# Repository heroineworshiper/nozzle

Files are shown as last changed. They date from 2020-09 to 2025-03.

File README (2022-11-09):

F-35 NOZZLE
Copyright (C) 2020-2022 Adam Williams <broadcast at earthling dot net>

This program is free software; you can redistribute it and/or modify
it under the terms of the GNU General Public License as published by
the Free Software Foundation; either version 2 of the License, or
(at your option) any later version.

This program is distributed in the hope that it will be useful,
but WITHOUT ANY WARRANTY; without even the implied warranty of
MERCHANTABILITY or FITNESS FOR A PARTICULAR PURPOSE.  See the
GNU General Public License for more details.

You should have received a copy of the GNU General Public License
along with this program; if not, write to the Free Software
Foundation, Inc., 59 Temple Place, Suite 330, Boston, MA  02111-1307  USA

What you'll find here:

nozzle.pcb - obsolete layout of the electronicals
nozzle.X - obsolete firmware for the electronicals

nozzle.c - atmega328 firmware for common motor controller
nozzle5.pcb - layout of common motor controller

export*.FCMacro: obsolete scripts

final.FCStd - print tube segments with motor attachments

monitor.c - dump debugging statements from serial port without motor polling commands

motor2.FCStd - latest motor assembly

base.FCStd - base + electronical platform

bearing2.FCStd - latest bearing parts.  
    Mane gear must be 2 parts to be installed.
    Print mane gear ORed with print mask.  Print mask must be rotated 180 deg 
    not cut in order to get the horizontal expansion gap.
    Print bearing inner, bearing outer

tube.c - generate isogrid tubes

elbow1.FCStd: model for elbow1 & elbow3 segments
 - the 2 elbow segments with motors use identical tube sections
 - must transfer to final.FCStd & print with motor mounts
 - subtract inside from motor mount but don't print it
 - remove support after printing

elbow2.FCStd: print to get elbow2
    - support is on opposite side as elbow1
    - remove support after printing
    - must glue elbow2 & elbow3 so the short & long sides line up

exit.c - generate the exit nozzle to be combined with exit.FCStd
    Run exit to generate exit.stl

exit.FCSTd:
    - print tube & exit separately from here
    - remove support after printing
    - clip off chevron support

final.FCStd: print segments with motors from here
    - inlet + inlet motor mount
    - elbow1 + elbow1 motor mount
    - elbow3 + elbow3 motor mount
    - other segments are only shown to aid alignment
    - must glue elbow2 & elbow3 so the short & long sides line up

inlet.FCStd: model for inlet segment
    - must transfer to final.FCStd & print with motor mount

3dstuff.h - common 3D functions

--------------------------------------------------------------------------------
Programming the common motor controller:

Set the board number in nozzle.h
make clean

Program the bootloader
make nozzle_fuse
make bootloader_isp

--------------------------------------------------------------------------------
Previous notes:

This design used leftover motors without encoders from polulu.  An
easier design would use gearmotors with built in encoders from
adafruit.com.  Lighter motors are better.  100:1 or more is better.

The latest versions of each part are listed here.
25% infill

standalone motor parts:
     - print with no raft
     - 50% infill
     - Support must be everywhere instead of just touching base
    motor2.FCStd
        pinion
        top platform
        strap
         - Print the laminations perpendicular to the motor axis

tubes with motor parts:
    final.FCStd
        inlet
        elbows
        oblique or straight bottom base depending on the tube section
        tube section
         - Tubes must be printed with the tapered overhang on top.
         - Print with a brim & support to aid the 1mm alignment rings
        cable guards
         - Only needed for 2 motors.
         - hot glued on
         - Print the laminations perpendicular to the motor axis
         - use a brim to aid separating the support

bearing parts:
     - print with no raft or support to get flat sides
    bearing.FCStd
        split mane gear with 2 different gear splitters to get 2 halves
        bearing inner
        bearing outer

base:
    no support
    skirt adhesion
    base.FCStd
        base
        electronicals + screw holes

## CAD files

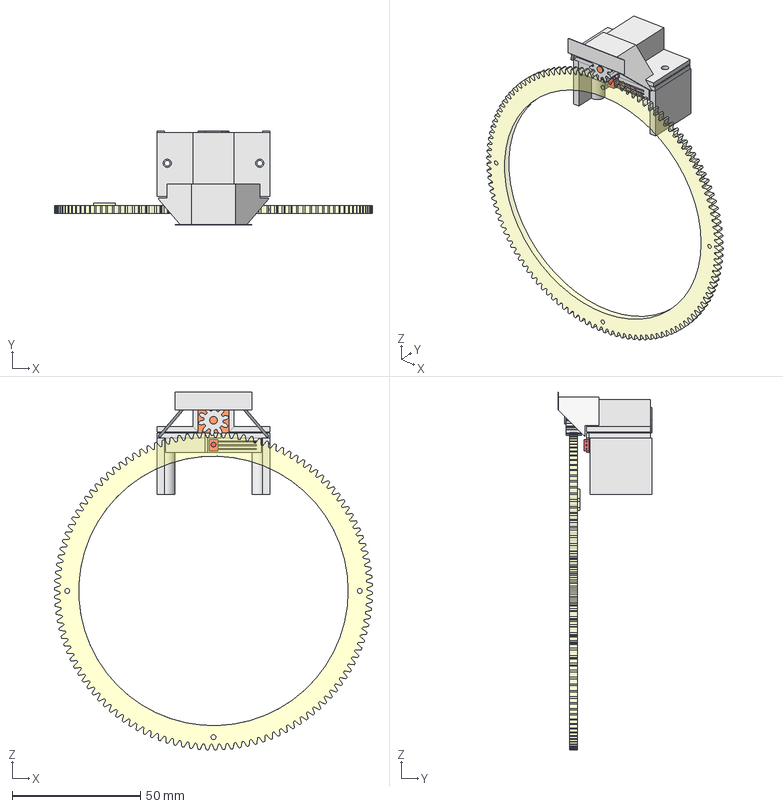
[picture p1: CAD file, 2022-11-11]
motor2.FCStd
124.0 x 36.5 x 139.5 mm
motor001
pinion gear
hall006
mane gear
cable shroud
motor strap
motor stand
motor base

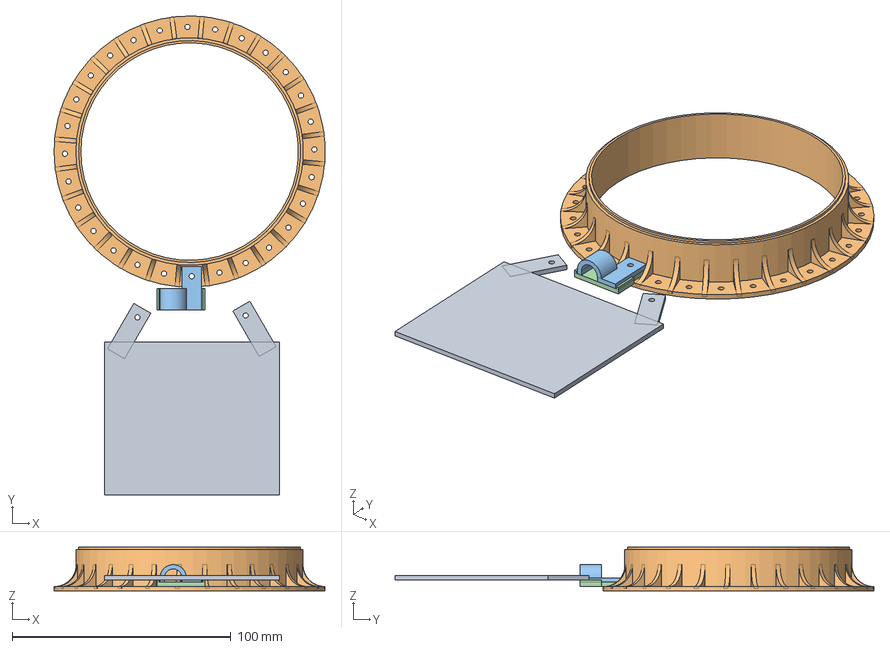
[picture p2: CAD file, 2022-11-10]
base.FCStd
123.9 x 219.0 x 20.0 mm
electronicals + screw holes
base
cable1
cable2

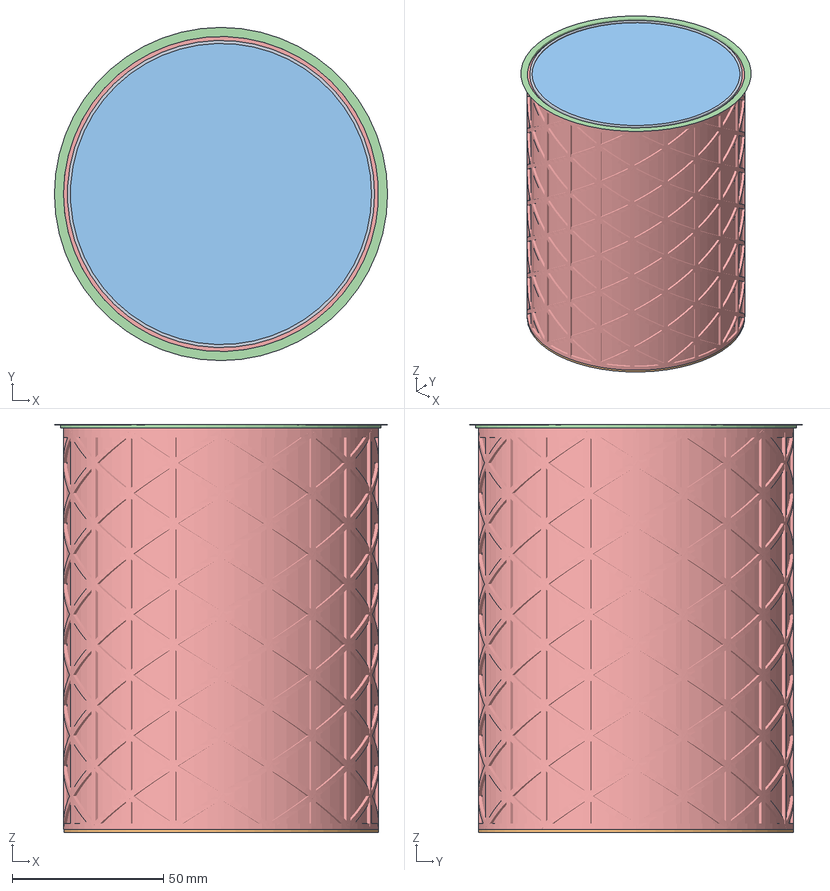
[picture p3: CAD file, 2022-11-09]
inlet.FCStd
110.0 x 110.0 x 134.7 mm
Thickness
overlap015
inside
support
inlet

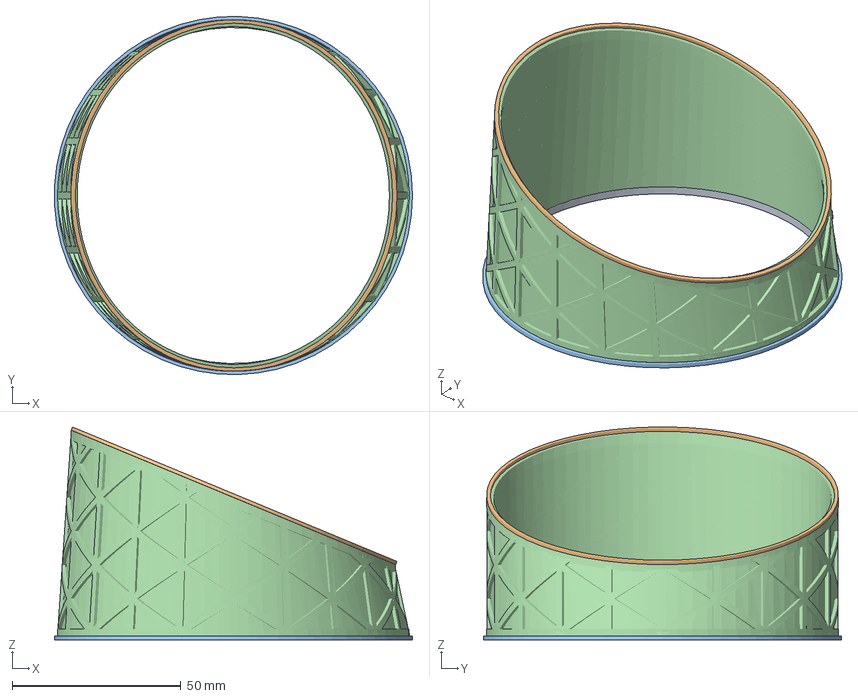
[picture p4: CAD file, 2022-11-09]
elbow2.FCStd
105.9 x 106.0 x 63.0 mm
overlap002
overlap001
support001
elbow

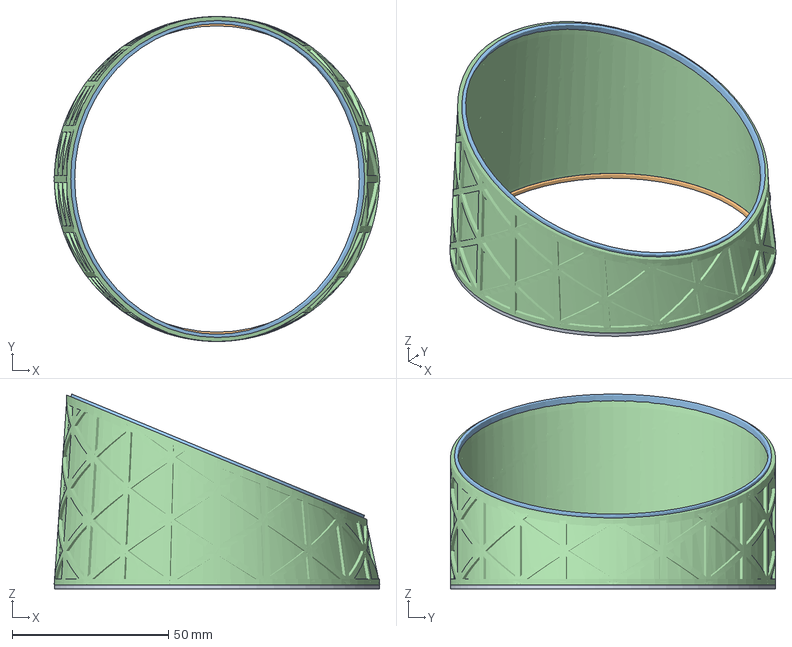
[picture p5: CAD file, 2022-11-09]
elbow1.FCStd
104.2 x 104.0 x 62.4 mm
overlap001
support
elbow

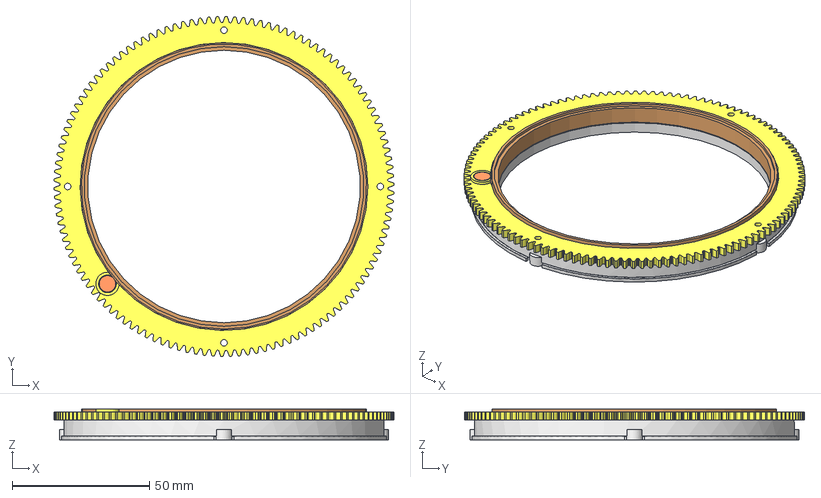
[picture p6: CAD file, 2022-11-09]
bearing2.FCStd
124.0 x 124.0 x 11.2 mm
mane gear
magnet002
bearing inner001
bearing outer003

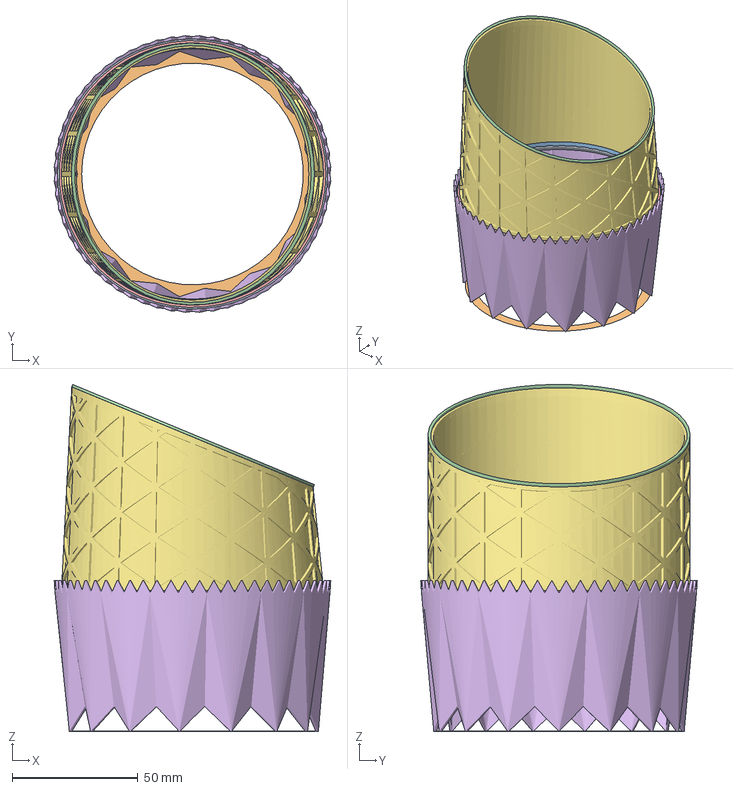
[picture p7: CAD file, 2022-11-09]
exit.FCStd
109.8 x 109.8 x 137.8 mm
support001
overlap009
overlap008
exit003
outlet

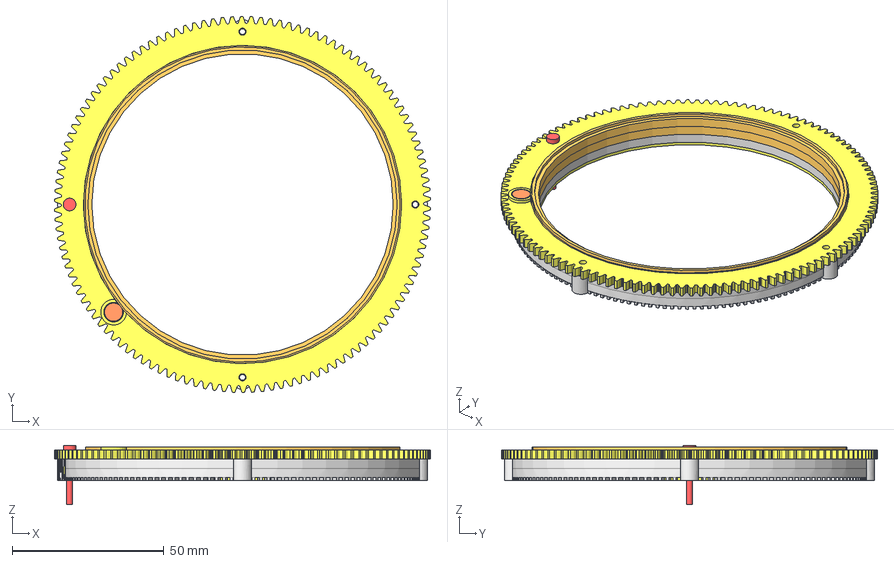
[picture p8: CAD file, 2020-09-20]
bearing.FCStd
124.0 x 124.0 x 19.6 mm
screw001
mane gear
magnet002
bottom thickness
top thickness
top overlap
bottom overlap
strut
bearing outer + screw holes

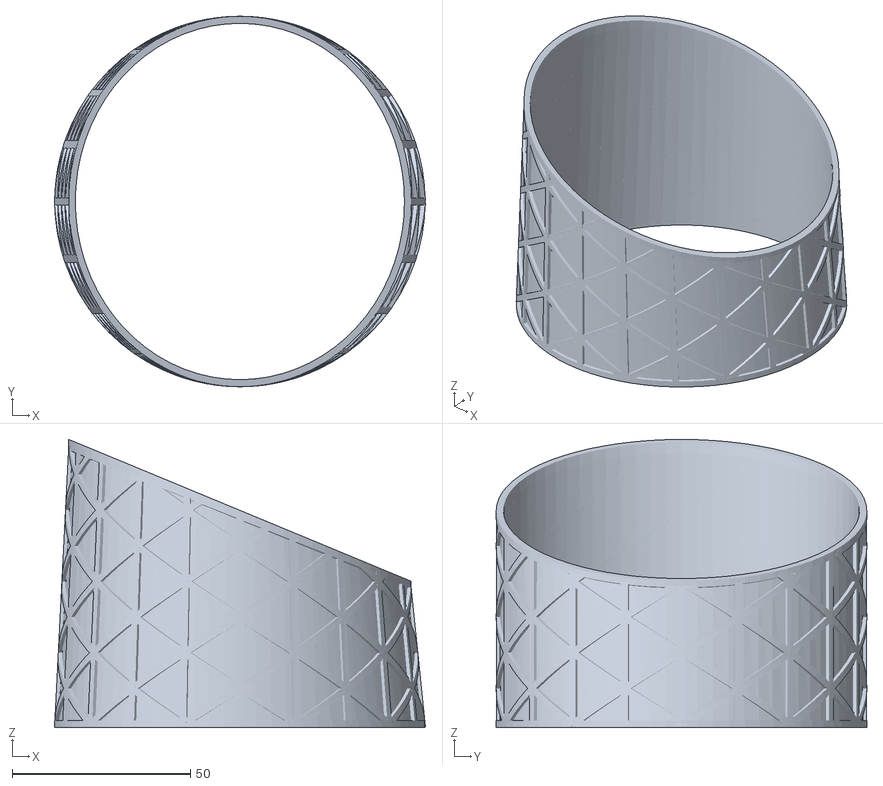
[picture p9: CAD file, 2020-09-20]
outlet.stl
104.1 x 104.0 x 80.9

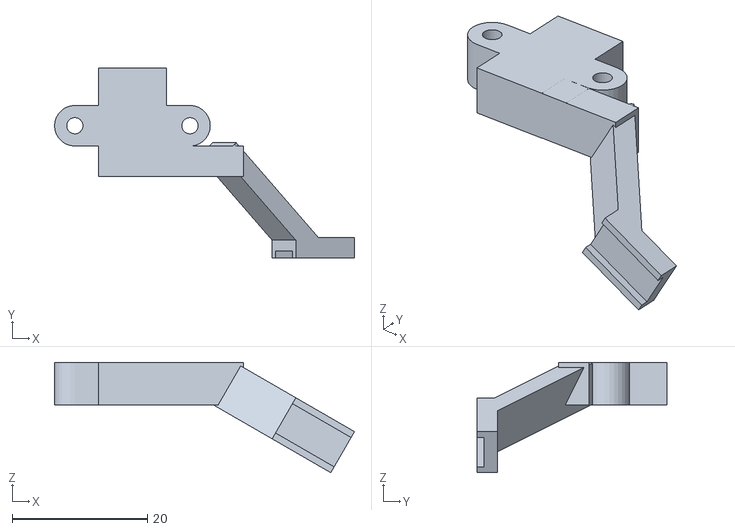
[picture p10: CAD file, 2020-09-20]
top_base.stl
44.3 x 28.0 x 16.3

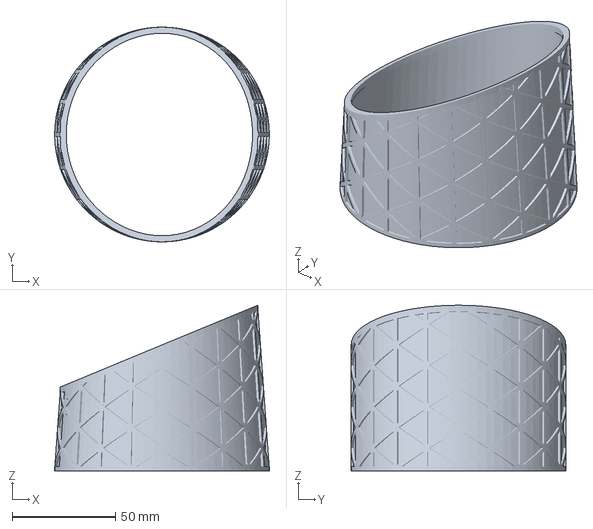
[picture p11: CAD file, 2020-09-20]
elbow4.3mf
104.1 x 104.0 x 80.2 mm

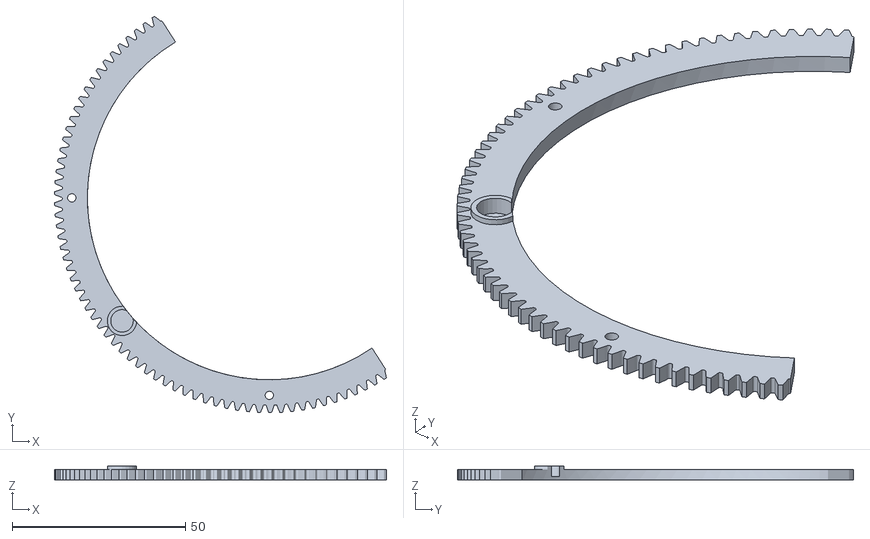
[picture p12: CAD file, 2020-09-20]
mane_gear1.stl
95.8 x 114.4 x 4.00

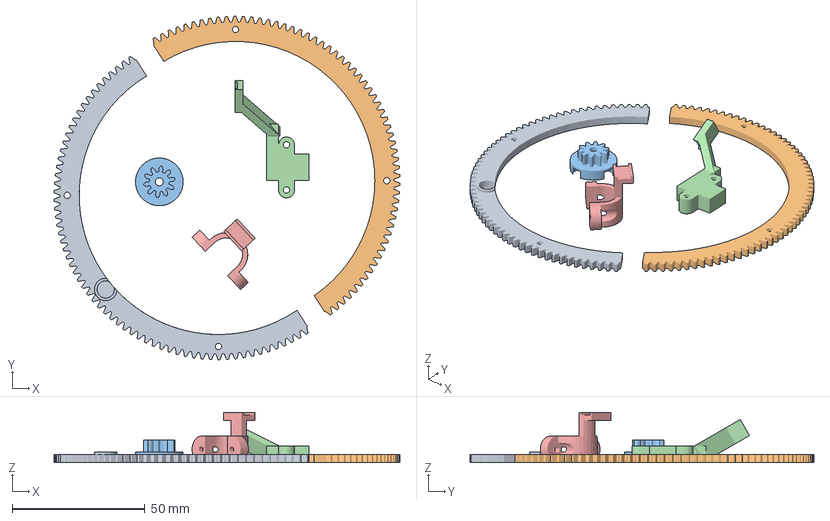
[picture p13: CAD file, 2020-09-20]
mane_gear.3mf
130.5 x 129.5 x 19.0 mm
mane_gear1.stl
mane_gear2.stl
pinion.stl
top_platform.stl
strap.stl

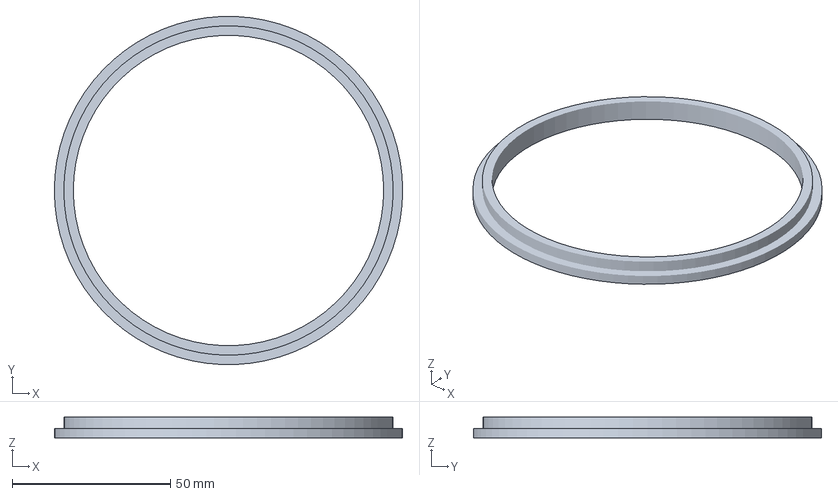
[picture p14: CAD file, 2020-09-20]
bearinginner.3mf
110.0 x 109.9 x 6.50 mm

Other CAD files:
top_platform.stl
bearingouter.stl
cableguard.stl
electronicals.stl
base.stl
bearinginner.stl
bodge.stl
bottom_base.stl
elbow.FCStd
elbow.stl
elbow1.3mf
elbow1.stl
elbow2.3mf
elbow2.stl
elbow3.3mf
elbow3.stl
elbow4.stl
exit.3mf
exit.stl
exit_elbow.stl
hall.FCStd
inlet.3mf
inlet.stl
mane_gear.stl
mane_gear2.stl
motor.FCStd
strap.stl
test.stl
tube.stl
tube2.stl

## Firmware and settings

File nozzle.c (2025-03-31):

/*
 * F-35 COMMON NOZZLE BOARD
 * Copyright (C) 2020-2025 Adam Williams <broadcast at earthling dot net>
 * 
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
 */

// this runs on each control board
// make board0.hex
// make board1.hex
// make board2.hex
// make nozzle_fuse
// make board0_isp
// make board1_isp
// make board2_isp

// disable this to try to reduce encoder drift
//#define ENABLE_DEBUG
// disable this to actually see the debugging output
#define ENABLE_POLLING


#include "uart.h"
#include "nozzle.h"
#include "table.h"

#include <inttypes.h>
#include <avr/io.h>
#include <avr/pgmspace.h>
#include <avr/interrupt.h>
#include <avr/wdt.h>
#include <util/delay.h>

#define TOGGLE_LED PORTB ^= (1 << DDB5);
#define LED_DELAY (HZ / 2)
#define LED_DELAY2 (HZ / 4)

// boundary sensor
#define HALL_THRESHOLD 16
#define HALL_CENTER 127

// ticks to wait for a motor to stop
#define MOTOR_DELAY (HZ / 2)

#if BOARD == 0
// IR code follows.  Improved version of heroineclock 2
typedef struct
{
    const uint8_t *data;
    const uint8_t value;
} ir_code_t;

// remote control codes.  Discard 1st & last symbol received since we
// only capture the rising edge.
const uint8_t up_data[] = 
{ 4,4,1,4,1,1,1,1,4,1,4,1,4,4,4,4,1,4,4,4,1,1,4,1,4,1,1,1,4,4,1,4,1 };
const uint8_t down_data[] = 
{ 4,4,1,4,1,1,1,1,4,1,4,1,4,4,4,4,1,1,4,4,1,1,4,1,4,4,1,1,4,4,1,4,1 };
const uint8_t left_data[] = 
{ 4,4,1,4,1,1,1,1,4,1,4,1,4,4,4,4,1,1,1,4,4,1,4,1,4,4,4,1,1,4,1,4,1 };
const uint8_t right_data[] = 
{ 4,4,1,4,1,1,1,1,4,1,4,1,4,4,4,4,1,4,1,4,4,1,4,1,4,1,4,1,1,4,1,4,1 };
const uint8_t fastrev_data[] = 
{ 4,4,1,4,1,1,1,1,4,1,4,1,4,4,4,4,1,4,1,1,4,4,4,4,1,1,4,4,1,1,1,1,4 };
const uint8_t fastfwd_data[] = 
{ 4,4,1,4,1,1,1,1,4,1,4,1,4,4,4,4,1,4,4,1,1,1,4,4,1,1,1,4,4,4,1,1,4 };
const uint8_t num7_data[] = 
{ 4,4,1,4,1,1,1,1,4,1,4,1,4,4,4,4,1,4,4,1,4,1,4,4,4,1,1,4,1,4,1,1,1 };
const uint8_t num8_data[] = 
{ 4,4,1,4,1,1,1,1,4,1,4,1,4,4,4,4,1,1,4,1,4,1,4,1,4,4,1,4,1,4,1,4,1 };
const uint8_t num9_data[] = 
{ 4,4,1,4,1,1,1,1,4,1,4,1,4,4,4,4,1,1,1,1,4,4,4,4,1,4,4,4,1,1,1,1,4 };
const uint8_t num0_data[] = 
{ 4,4,1,4,1,1,1,1,4,1,4,1,4,4,4,4,1,1,4,1,4,4,4,4,1,4,1,4,1,1,1,1,4 };
const uint8_t top_right_data[] =
{ 4,4,1,4,1,1,1,1,4,1,4,1,4,4,4,4,1,4,1,4,1,1,4,4,4,1,4,1,4,4,1,1,1 };
const uint8_t top_left_data[] = 
{ 4,4,1,4,1,1,1,1,4,1,4,1,4,4,4,4,1,1,1,4,1,1,4,4,4,4,4,1,4,4,1,1,1 };
const uint8_t enter_data[] =
{ 4,4,1,4,1,1,1,1,4,1,4,1,4,4,4,4,1,4,1,4,4,1,4,4,4,1,4,1,1,4,1,1,1 };
const uint8_t clear_data[] =
{ 4,4,1,4,1,1,1,1,4,1,4,1,4,4,4,4,1,4,1,1,4,1,4,1,4,1,4,4,1,4,1,4,1 };



#define UP 0
#define DOWN 1
#define LEFT 2
#define RIGHT 3
#define POWER 4
#define SET_PRESET 5
#define PRESET1 6
#define PRESET2 7
#define PRESET3 8
#define PRESET4 9
#define PRESET5 12
#define PRESET6 13
#define TOP_LEFT 10
#define TOP_RIGHT 11


const ir_code_t ir_codes[] = { 
    { num7_data, PRESET1 },
    { num8_data, PRESET2 },
    { num9_data, PRESET3 },
    { num0_data, PRESET4 },
    { enter_data, PRESET5 },
    { clear_data, PRESET6 },
    { up_data,   UP },
	{ down_data,  DOWN },
	{ left_data,  LEFT },
	{ right_data, RIGHT },
    { fastfwd_data, SET_PRESET },
    { fastrev_data, POWER },
    { top_left_data, TOP_LEFT },
    { top_right_data, TOP_RIGHT },
};

#define CODE_SIZE sizeof(up_data)
uint8_t code_buffer[CODE_SIZE];
uint8_t polling_packet[3];

// ticks
// 120ms observed.
#define IR_TIMEOUT (120 * HZ / 1000)
#define TOTAL_CODES (sizeof(ir_codes) / sizeof(ir_code_t))
volatile uint8_t got_ir_int = 0;
volatile uint8_t ir_time = 0;
volatile uint8_t ir_timeout = 0;
uint8_t code_offset = 0;
// IR is transmitting repeats
uint8_t have_ir = 0;
// last IR code received
uint8_t ir_code = 0;
// repeating a code or 0xff
uint8_t repeating_code = 0xff;
// delay before 1st repeat
uint8_t repeat_delay = 0;
#define REPEAT_DELAY (HZ / 2)
#define REPEAT_DELAY2 (HZ / 4)
uint8_t first_edge = 1;



typedef struct
{
    int16_t pitch;
    int16_t angle;
} preset_t;

#define PRESETS 6
#define PRESET_DELAY (HZ / 2)
uint8_t setting_preset = 0;
uint8_t current_preset = 0;
preset_t presets[PRESETS];
void (*preset_state)() = 0;
int16_t orig_nozzle_yaw = 0;
uint8_t preset_delay = 0;



// motors are armed
uint8_t armed = 0;
// blinking
uint8_t led_counter = 0;

// current state of the home operation & the motor tracking
uint8_t current_motor = 0;

void motor_idle();
void motor_home1();
void (*motor_state)() = motor_idle;


// pitch of the nozzle in polar coordinates
int16_t nozzle_pitch = 0;
// user position of motor 0 to which the nozzle_pitch adds an offset to compensate
// for the nozzle bending sideways
int16_t nozzle_yaw = 0;

// encoder step of angle adjustments
#define YAW_STEP 100



#endif // BOARD == 0


#define TOTAL_MOTORS 3
typedef struct
{
// Analog value of the hall effect sensor
    uint8_t boundary;
// encoder accumulator
    int16_t encoder;
// encoder sign.  - is towards the boundary
    int8_t sign;

// H bridge bitmasks of the 2 directions
    uint8_t dec_mask; // go towards boundary
    uint8_t inc_mask; // go away from boundary
    uint8_t total_unmask; // motor_master bits for coasting
    uint8_t total_mask; // motor_master bits for breaking

// ticks remaneing to sleep
    uint8_t timer;
    int16_t target_position;
// only move the motors if this is > 0
    uint16_t changed;
    uint8_t homing;
} tracking_state_t;
tracking_state_t tracking_state[TOTAL_MOTORS];


// raw encoder data
uint8_t prev_encoder = 0;
int8_t encoder_count = 0;

// raw boundary sensor data
uint8_t adc_downsample = 0;
#define ADC_DOWNSAMPLE 64
uint16_t adc_accum = 0;

uint8_t status_packet[4];
//uint8_t status_delay;
//uint8_t want_status = 0;
void (*receive_state)();
uint8_t receive_board = 0;
// poll every other tick
#define POLLING_DELAY 2
// test interleaved debugging output
//#define POLLING_DELAY 4
uint8_t polling_delay = POLLING_DELAY;
uint8_t polling_board = 1;
uint8_t debug_counter = 0;

#define MOTOR_TIMEOUT HZ
uint8_t motor_timeout = 0;

// state of all H bridge pins
uint8_t motor_master = 0;
#define MOTOR2_RIGHT (uint8_t)0b00100000
#define MOTOR2_LEFT  (uint8_t)0b00010000
#define MOTOR1_RIGHT (uint8_t)0b00001000
#define MOTOR1_LEFT  (uint8_t)0b00000100
#define MOTOR0_RIGHT (uint8_t)0b00000010
#define MOTOR0_LEFT  (uint8_t)0b00000001
#define TOTAL_MASK 0b00111111


#if BOARD == 0
#define HANDLE_ENCODER0 \
    tracking_state[0].encoder += encoder_count * tracking_state[0].sign; \
    encoder_count = 0;
#else
#define HANDLE_ENCODER0 ;
#endif


#define HANDLE_ENCODERS \
{ \
    uint8_t current_encoder = PINC & 0b00001100; \
    if(current_encoder != prev_encoder) \
    { \
        if(current_encoder == 0b00001000 && \
            prev_encoder == 0b00001100) \
        { \
            encoder_count++; \
        } \
        else \
        if(current_encoder == 0b00001100 && \
            prev_encoder == 0b00001000) \
        { \
            encoder_count--; \
        } \
        prev_encoder = current_encoder; \
 \
        HANDLE_ENCODER0 \
 \
/* print_number(bitRead(PINC, 2)); */ \
/* print_number(bitRead(PINC, 3)); */ \
/* print_number(encoder_count); */ \
/* print_text("\n"); */ \
    } \
}

#if BOARD == 0

#ifdef ENABLE_DEBUG
void print_status()
{
//     print_text("BOARD0: ");
//     print_number(tracking_state[0].encoder);
//     print_number(tracking_state[0].boundary);
//     print_text("BOARD1: ");
//     print_number(tracking_state[1].encoder);
//     print_number(tracking_state[1].boundary);
//     print_text("BOARD2: ");
//     print_number(tracking_state[2].encoder);
//     print_number(tracking_state[2].boundary);
//     print_text("YAW=");
//     print_number(nozzle_yaw);
//     print_text("PITCH=");
//     print_number(nozzle_pitch);
//     print_text("\n");
}
#else
#define print_status() \
    ;
#endif


// update the tracking states to get the desired nozzle pitch & roll
void update_motors()
{
    int16_t prev_positions[TOTAL_MOTORS];
    uint8_t i;

    for(i = 0; i < TOTAL_MOTORS; i++)
        prev_positions[i] = tracking_state[i].target_position;

    prev_positions[0] = tracking_state[0].target_position;
    prev_positions[1] = tracking_state[1].target_position;
    prev_positions[2] = tracking_state[2].target_position;

    CLAMP(nozzle_pitch, 0, PITCH_STEPS);
// TODO: add pitch table to get yaw encoder value
    tracking_state[0].target_position = nozzle_yaw + 
        pitch_to_encoders[nozzle_pitch * 3 + 0];
    tracking_state[1].target_position = pitch_to_encoders[nozzle_pitch * 3 + 1];
    tracking_state[2].target_position = pitch_to_encoders[nozzle_pitch * 3 + 2];

// Only move the changed motors, since the encoders aren't precise
    for(i = 0; i < TOTAL_MOTORS; i++)
    {
        if(prev_positions[i] != tracking_state[i].target_position &&
            tracking_state[i].changed < 0xff)
            tracking_state[i].changed++;
    }
}

// return 1 if the motors are tracking
// uint8_t motors_tracking()
// {
//     if(tracking_state[0].changed > 0 ||
//         tracking_state[1].changed > 0 ||
//         tracking_state[2].changed > 0)
//     {
//         return 1;
//     }
//     return 0;
// }

#define MOTORS_TRACKING \
    (tracking_state[0].changed > 0 || \
        tracking_state[1].changed > 0 || \
        tracking_state[2].changed > 0)

void motor_tracking()
{
// only enough clockcycles to test 1 motor per iteration
    tracking_state_t *tracking = &tracking_state[current_motor];
    uint8_t i;

    current_motor++;
    if(current_motor >= TOTAL_MOTORS)
    {
        current_motor = 0;
    }


#define YAW_REPEATING (repeating_code == LEFT || repeating_code == RIGHT)
    
// motor moving up
    if((motor_master & tracking->total_mask) == tracking->inc_mask)
    {
        if(!YAW_REPEATING && tracking->encoder >= tracking->target_position)
        {
// brake if it hit the target position & it's not an IR repeat
            motor_master |= tracking->total_mask;
        }
    }
    else
    if((motor_master & tracking->total_mask) == tracking->dec_mask)
    {
// motor moving down
        if(!YAW_REPEATING && tracking->encoder <= tracking->target_position)
        {
// brake if it hit the target position & it's not an IR command
            motor_master |= tracking->total_mask;
        }
    }
    else
// process the next command
    if(tracking->changed > 0)
    {
// print_text("changed=");
// print_number(tracking->changed);
// print_text("\n");
        if(tracking->encoder > tracking->target_position)
        {
// move motor down
            motor_master &= tracking->total_unmask;
            motor_master |= tracking->dec_mask;
            tracking->changed--;
        }
        else
        if(tracking->encoder < tracking->target_position)
        {
// move motor down
            motor_master &= tracking->total_unmask;
            motor_master |= tracking->inc_mask;
            tracking->changed--;
        }
        else
        {
// no difference in position.  Cancel the loop.
            tracking->changed--;
        }
    }
    else
// process a pitch repeat once all the motors are stopped
// the preset reader does this in preset_state, outside motor_tracking.
    if(repeating_code == UP && (motor_master & TOTAL_MASK) == TOTAL_MASK)
    {
        if(nozzle_pitch > 0)
        {
            nozzle_pitch--;
// assume the direction of the motors is 1 way & don't back up
            for(i = 0; i < TOTAL_MOTORS; i++)
            {
                int16_t new_position = pitch_to_encoders[nozzle_pitch * 3 + i];
                if(i == 0) new_position += nozzle_yaw;
                if(new_position < tracking_state[i].encoder)
                {
                    tracking_state[i].target_position = new_position;
// update the H bridge before it drifts past the target position
                    motor_master &= tracking_state[i].total_unmask;
                    motor_master |= tracking_state[i].dec_mask;
                }
            }
        }
    }
    else
    if(repeating_code == DOWN && (motor_master & TOTAL_MASK) == TOTAL_MASK)
    {
        if(nozzle_pitch < PITCH_STEPS)
        {
            nozzle_pitch++;
// assume the direction of the motors is 1 way & don't back up
            for(i = 0; i < TOTAL_MOTORS; i++)
            {
                int16_t new_position = pitch_to_encoders[nozzle_pitch * 3 + i];
                if(i == 0) new_position += nozzle_yaw;
                if(new_position > tracking_state[i].encoder)
                {
                    tracking_state[i].target_position = new_position;
// update the H bridge before it drifts past the target position
                    motor_master &= tracking_state[i].total_unmask;
                    motor_master |= tracking_state[i].inc_mask;
                }
            }
        }
    }
}


// wait a while
void motor_home6()
{
    tracking_state_t *tracking = &tracking_state[current_motor];
    if(tracking->timer == 0)
    {
        uint8_t current_encoder = tracking->encoder;

        switch(current_motor)
        {
            case 2:
                current_motor = 1;
                motor_state = motor_home1;
                break;
            case 1:
                current_motor = 0;
                motor_state = motor_home1;
                break;
            case 0:
            default:
                current_motor = 0;
                motor_state = motor_tracking;
// pitch is always 0 after homing
                nozzle_yaw = tracking->target_position;
                print_status();
                break;
        }
    }
}

// wait until home position
void motor_home5()
{
    tracking_state_t *tracking = &tracking_state[current_motor];
    if(tracking->encoder >= tracking->target_position)
    {
// brake
        motor_master |= tracking->total_mask;

        tracking->timer = MOTOR_DELAY;
        motor_state = motor_home6;
    }
}

// go until boundary is detected again
void motor_home4()
{
    tracking_state_t *tracking = &tracking_state[current_motor];
    if(ABS(tracking->boundary - HALL_CENTER) >= HALL_THRESHOLD)
    {
// reset encoder
        tracking->encoder = 0;
        motor_state = motor_home5;
    }
}

// reverse
void motor_home3()
{
    tracking_state_t *tracking = &tracking_state[current_motor];
    if(ABS(tracking->boundary - HALL_CENTER) < HALL_THRESHOLD)
    {
// always coast
        motor_master &= tracking->total_unmask;
        motor_master |= tracking->inc_mask;
        motor_state = motor_home4;
    }
}

// detect motor boundary & overshoot
void motor_home2()
{
    tracking_state_t *tracking = &tracking_state[current_motor];
    if(ABS(tracking->boundary - HALL_CENTER) >= HALL_THRESHOLD)
    {
        motor_state = motor_home3;
    }
}

// go to home position
void motor_home1()
{
    tracking_state_t *tracking = &tracking_state[current_motor];
    uint8_t sensor_value = tracking->boundary;
// sensor is already on boundary.  Abort.
// It can't arm if any sensors are on their boundary.
    if(ABS(tracking->boundary - HALL_CENTER) >= HALL_THRESHOLD)
    {
        motor_state = motor_idle;
    }
    else
// command motor to move to boundary
    {
        motor_master &= tracking->total_unmask;
        motor_master |= tracking->dec_mask;
        motor_state = motor_home2;
    }
}
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
void main()
{
    uint8_t i;

// disable watchdog
	WDTCSR = 0;

	init_serial();
#if BOARD == 0
	print_text("\n\nWelcome to F-35 nozzle\n");
#endif

#if BOARD == 1
	print_text("\n\nWelcome to board 1\n");
#endif

#if BOARD == 2
	print_text("\n\nWelcome to board 2\n");
#endif

// motor H bridge
    bitClear(PORTD, 3);
    bitClear(PORTD, 4);
    bitSet(DDRD, 3);
    bitSet(DDRD, 4);


// LED/DEBUG
    DDRB |= 1 << DDB5;
    LED_ON

// tick clock prescaler page 108
// CLKio is 32khz
    TCCR0B = 0b00000100;

#if BOARD == 0


// enable IR interrupt page 72
    EIMSK = 0b00000001;
// rising edge interrupt page 71
    EICRA = 0b00000011;
// enable IR timer page 156
    TCCR2B = 0b00000100;

// initialize motor tables
    for(i = 0; i < TOTAL_MOTORS; i++)
    {
        tracking_state[i].boundary = HALL_CENTER;
        tracking_state[i].encoder = 0;
    }

    tracking_state[2].dec_mask = MOTOR2_LEFT;
    tracking_state[2].inc_mask = MOTOR2_RIGHT;
    tracking_state[2].total_unmask = ~(MOTOR2_LEFT | MOTOR2_RIGHT);
    tracking_state[2].total_mask = MOTOR2_LEFT | MOTOR2_RIGHT;
    tracking_state[2].sign = 1;

    tracking_state[1].dec_mask = MOTOR1_RIGHT;
    tracking_state[1].inc_mask = MOTOR1_LEFT;
    tracking_state[1].total_unmask = ~(MOTOR1_LEFT | MOTOR1_RIGHT);
    tracking_state[1].total_mask = MOTOR1_LEFT | MOTOR1_RIGHT;
    tracking_state[1].sign = -1;

    tracking_state[0].dec_mask = MOTOR0_LEFT;
    tracking_state[0].inc_mask = MOTOR0_RIGHT;
    tracking_state[0].total_unmask = ~(MOTOR0_LEFT | MOTOR0_RIGHT);
    tracking_state[0].total_mask = MOTOR0_LEFT | MOTOR0_RIGHT;
    tracking_state[0].sign = 1;

#endif // BOARD == 0

// boundary sensor page 249
    ADMUX = 0b01000000;
    ADCSRA = 0b10000111;
    bitSet(ADCSRA, ADSC);


    receive_state = get_code1;

#if BOARD == 0
    read_presets();
#endif

// enable interrupts
	sei();


// delay before polling
#if BOARD == 0
    uint16_t delay = HZ;
#endif

// delay for each board's print
#if BOARD == 1
    uint16_t delay = HZ / 2;
#endif

#if BOARD == 2
    uint16_t delay = 0;
#endif

    while(delay > 0)
    {
// handle tick
        if(bitRead(TIFR0, TOV0))
        {
            bitSet(TIFR0, TOV0);
            delay--;
        }
    }


	while(1)
	{
		HANDLE_SERIAL
		if(have_uart_in)
		{
			have_uart_in = 0;

            receive_state();
		}

#if BOARD == 0
// handle tick
        if(bitRead(TIFR0, TOV0))
        {
            bitSet(TIFR0, TOV0);
// DEBUG
//            TOGGLE_LED

// update motor timers
            for(i = 0; i < TOTAL_MOTORS; i++)
            {
                tracking_state_t *tracking = &tracking_state[i];
                if(tracking->timer > 0)
                {
                    tracking->timer--;
                }
            }

            polling_delay--;
            if(polling_delay == 0)
            {
                polling_delay = POLLING_DELAY;
#ifdef ENABLE_POLLING
                polling_packet[0] = 0xff;
                polling_packet[1] = 0xa8 | polling_board;
                polling_packet[2] = motor_master;
                SEND_UART(polling_packet, 3);
#endif

                if(polling_board == 2)
                    polling_board = 1;
                else
                    polling_board = 2;
            }

// service the debug output in every tick we're not polling
#ifdef ENABLE_DEBUG
            if(polling_delay != POLLING_DELAY)
            {
                debug_counter++;
                if(debug_counter >= 10)
                {
                    debug_counter = 0;
// print the status
                    print_status();
                }
                handle_debug();
            }
#endif

            if(ir_timeout > 0) ir_timeout--;


            if(!armed)
            {
                led_counter++;
                if(led_counter >= LED_DELAY)
                {
                    led_counter = 0;
                    
// toggle it if unarmed & no motors are being tested
                    if(motor_master == 0)
                        TOGGLE_LED
                }
            }
            else
            if(setting_preset || preset_state != 0)
            {
                led_counter++;
                if(led_counter >= LED_DELAY2)
                {
                    led_counter = 0;
                    TOGGLE_LED
                }
            }


            if(repeat_delay > 0) repeat_delay--;
            if(preset_delay > 0) preset_delay--;
        }

        motor_state();

        HANDLE_IR

        if(preset_state != 0 && !MOTORS_TRACKING)
            preset_state();
#else // BOARD 0



// handle tick
        if(bitRead(TIFR0, TOV0))
        {
            bitSet(TIFR0, TOV0);

#ifdef ENABLE_DEBUG
            handle_debug();
#endif

// shut down if no packet received
            if(motor_timeout == 0)
                motor_master = 0;
            else
                motor_timeout--;

//             if(want_status)
//             {
//                 if(status_delay > 0)
//                     status_delay--;
//                 else
//                 {
//                     want_status = 0;
//                     SEND_UART(status_packet, 4);
//                 }
//             }
        }
#endif // BOARD != 0


        HANDLE_ENCODERS


// boundary sensor        
        if(bitRead(ADCSRA, ADIF))
        {
            bitSet(ADCSRA, ADIF);
// must read the right byte order to update the registers
            uint8_t low = ADCL;
            uint8_t high = ADCH;
            adc_accum += (high << 8) | low;
            adc_downsample++;
            if(adc_downsample >= ADC_DOWNSAMPLE)
            {
//print_number(adc_accum / ADC_DOWNSAMPLE);
//print_text("\n");
                tracking_state[BOARD].boundary = adc_accum / ADC_DOWNSAMPLE / 4;
                adc_accum = 0;
                adc_downsample = 0;
            }
            bitSet(ADCSRA, ADSC);
        }


// update motors
#if BOARD == 0
        bitWrite(PORTD, 3, (motor_master & MOTOR0_LEFT));
        bitWrite(PORTD, 4, (motor_master & MOTOR0_RIGHT));
#endif

#if BOARD == 1
        bitWrite(PORTD, 3, (motor_master & MOTOR1_LEFT));
        bitWrite(PORTD, 4, (motor_master & MOTOR1_RIGHT));
#endif

#if BOARD == 2
        bitWrite(PORTD, 3, (motor_master & MOTOR2_LEFT));
        bitWrite(PORTD, 4, (motor_master & MOTOR2_RIGHT));
#endif
    }
}

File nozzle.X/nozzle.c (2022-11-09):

/*
 * F-35 NOZZLE CONTROLLER
 * Copyright (C) 2020-2022 Adam Williams <broadcast at earthling dot net>
 * 
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
 */

// B0 - IR input
// B4 - power button
// AN0-AN5 - hall sensors
// D7 - LED
// D0-D5 - H bridges

// PORTC is dead on the recycled chip


// CONFIG
#pragma config FOSC = HS        // Oscillator Selection bits (HS oscillator)
#pragma config WDTE = ON        // Watchdog Timer Enable bit (WDT enabled)
#pragma config PWRTE = OFF      // Power-up Timer Enable bit (PWRT disabled)
#pragma config BOREN = ON       // Brown-out Reset Enable bit (BOR enabled)
#pragma config LVP = OFF        // Low-Voltage (Single-Supply) In-Circuit Serial Programming Enable bit (RB3 is digital I/O, HV on MCLR must be used for programming)
#pragma config CPD = OFF        // Data EEPROM Memory Code Protection bit (Data EEPROM code protection off)
#pragma config WRT = OFF        // Flash Program Memory Write Enable bits (Write protection off; all program memory may be written to by EECON control)
#pragma config CP = OFF         // Flash Program Memory Code Protection bit (Code protection off)


#include <pic16f877a.h>
#include <stdint.h>
#include <string.h>
#include "nozzle.h"

// control motors using console input.  Disable if the serial port is floating.
//#define TEST_MODE
// less accurate motor positioning but more debugging output
//#define VERBOSE

// use XY control instead of polar
//#define XY_CONTROL

#define ABS(x) ((x) < 0 ? (-(x)) : (x))

//#define CLOCKSPEED 13300000
#define CLOCKSPEED 22579000
#define LED_TRIS TRISDbits.TRISD7
#define LED_PORT PORTDbits.RD7

#define HBRIDGE_MASK (uint8_t)0b00111111
#define HBRIDGE_PORT PORTD
#define HBRIDGE_TRIS TRISD
#define MOTOR2_RIGHT (uint8_t)0b00000010
#define MOTOR2_LEFT  (uint8_t)0b00000001
#define MOTOR1_RIGHT (uint8_t)0b00010000
#define MOTOR1_LEFT  (uint8_t)0b00100000
#define MOTOR0_RIGHT (uint8_t)0b00001000
#define MOTOR0_LEFT  (uint8_t)0b00000100

// coast instead of brake
//#define COAST

#define BUTTON_PORT PORTBbits.RB4

uint8_t have_serial = 0;
uint8_t serial_in = 0;
// page 115
#define BAUD_CODE (CLOCKSPEED / 16 / 57600)
uint8_t interrupt_done = 0;

#define UART_BUFSIZE 64
uint8_t uart_buffer[UART_BUFSIZE];
uint8_t uart_size = 0;
uint8_t uart_position1 = 0;
uint8_t uart_position2 = 0;

// motors are armed
uint8_t armed = 0;
uint8_t led_counter = 0;
// mane timer fires at 10Hz
#define HZ 100
#define TIMER1_VALUE (-CLOCKSPEED / 4 / 8 / HZ)
#define LED_DELAY (HZ / 2)
#define LED_DELAY2 (HZ / 4)

uint8_t got_tick = 0;
uint8_t tick = 0;

// current state of the home operation & the motor tracking
uint8_t current_motor = 0;


// copy of H bridge pins written by the user
uint8_t motor_master = 0;
// ticks to wait for a motor to stop
#define MOTOR_DELAY (HZ / 2)



uint8_t current_adc = 0;
#define ADCON0_MASK 0b10000001
#define TOTAL_ADC 6
#define TOTAL_MOTORS 3
#define BOUNDARY0 1 // nearest motor
#define BOUNDARY1 2
#define BOUNDARY2 5 // farthest motor
#define ENCODER0 0 // nearest motor
#define ENCODER1 3
#define ENCODER2 4 // farthest motor
// amount above or below 0x80
#define SENSOR_THRESHOLD 0x20

typedef struct 
{
// analog value
    uint8_t analog;
// last detected direction
    uint8_t ns;
// add or subtract steps from position if an encoder
    int8_t step;
// absolute position if an encoder
    int8_t position;
} sensor_state_t;
sensor_state_t sensors[TOTAL_ADC];

typedef struct
{
// ADC channel of the sensors
    uint8_t boundary;
    uint8_t encoder;
// H bridge bitmasks of the 2 directions
    uint8_t dec_mask; // go towards boundary
    uint8_t inc_mask; // go away from boundary
    uint8_t total_unmask; // coasting
    uint8_t total_mask; // breaking

// ticks remaneing to sleep
    uint8_t timer;
    int16_t target_position;
// position range
    int16_t min;
    int16_t max;
// only move the motors if this is > 0
    uint16_t changed;
// use the brake instead of coasting.  Outlet is light enough to use braking.
    uint8_t brake;
} tracking_state_t;
tracking_state_t tracking_state[TOTAL_MOTORS];


// pitch of the nozzle in polar coordinates
int16_t nozzle_pitch = 0;
// user position of motor 0 to which the nozzle_pitch adds an offset to compensate
// for the nozzle bending sideways
int16_t nozzle_angle = 0;

#ifdef XY_CONTROL
// nozzle direction in XY coordinates
int16_t nozzle_x = 0;
int16_t nozzle_y = 0;

// neighboring nozzle positions in XY
#define NEIGHBORS 4
int16_t neighbor_x[NEIGHBORS];
int16_t neighbor_y[NEIGHBORS];
uint8_t good_neighbors[NEIGHBORS];
// relative angle/pitch of neighboring nozzle positions
const int8_t neighbor_pitch[] = {  0, 0, -1, 1 };
const int8_t neighbor_angle[] = { -1, 1,  0, 0 };
#endif // XY_CONTROL


typedef struct
{
    int16_t pitch;
    int16_t angle;
} preset_t;

// location in EEPROM of presets
#define DATA_EE_ADDR 0x00
#define PRESETS 4
#define PRESET_DELAY (HZ / 2)
uint8_t setting_preset = 0;
uint8_t current_preset = 0;
preset_t presets[PRESETS];
void (*preset_state)() = 0;
int16_t orig_nozzle_angle = 0;
uint8_t preset_delay = 0;




// IR code follows.  Improved version of heroineclock 2
typedef struct
{
    const uint8_t *data;
	const uint8_t size;
    const uint8_t value;
} ir_code_t;

// remote control codes
const uint8_t up_data[] = 
{
    0x30, 0x19, 0x03, 0x02, 0x03, 0x09, 0x03, 0x02, 0x03, 0x09, 0x03, 0x09, 0x03, 0x09, 0x03, 0x09, 0x03, 0x03, 0x03, 0x09, 0x03, 0x03, 0x03, 0x09, 0x03, 0x03, 0x03, 0x03, 0x03, 0x03, 0x03, 0x03, 0x03, 0x09, 0x03, 0x02, 0x03, 0x02, 0x03, 0x03, 0x03, 0x09, 0x03, 0x09, 0x03, 0x03, 0x03, 0x09, 0x03, 0x03, 0x03, 0x09, 0x03, 0x09, 0x03, 0x09, 0x03, 0x03, 0x03, 0x03, 0x03, 0x09, 0x03, 0x03, 0x03, 0x09, 0x03, 0xdb, 0x30, 0x0b, 0x03 
};

const uint8_t down_data[] = 
{ 
    0x30, 0x19, 0x03, 0x02, 0x03, 0x09, 0x03, 0x03, 0x03, 0x09, 0x03, 0x09, 0x03, 0x09, 0x03, 0x09, 0x03, 0x03, 0x03, 0x09, 0x03, 0x03, 0x03, 0x09, 0x03, 0x03, 0x03, 0x03, 0x03, 0x03, 0x03, 0x03, 0x03, 0x09, 0x03, 0x09, 0x03, 0x02, 0x03, 0x03, 0x03, 0x09, 0x03, 0x09, 0x03, 0x03, 0x03, 0x09, 0x03, 0x03, 0x03, 0x02, 0x03, 0x09, 0x03, 0x09, 0x03, 0x02, 0x03, 0x03, 0x03, 0x09, 0x03, 0x02, 0x03, 0x09, 0x03, 0xdb, 0x30, 0x0c, 0x03
};

const uint8_t left_data[] =  
{
    0x30, 0x19, 0x03, 0x02, 0x03, 0x09, 0x03, 0x03, 0x03, 0x09, 0x03, 0x09, 0x03, 0x09, 0x03, 0x09, 0x03, 0x03, 0x03, 0x09, 0x03, 0x03, 0x03, 0x09, 0x03, 0x02, 0x03, 0x03, 0x03, 0x03, 0x03, 0x03, 0x03, 0x09, 0x03, 0x09, 0x03, 0x09, 0x03, 0x03, 0x03, 0x03, 0x03, 0x09, 0x03, 0x03, 0x03, 0x09, 0x03, 0x02, 0x03, 0x03, 0x03, 0x03, 0x03, 0x09, 0x03, 0x09, 0x03, 0x03, 0x03, 0x09, 0x03, 0x03, 0x03, 0x09, 0x03, 0xdb, 0x30, 0x0b, 0x03
};
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

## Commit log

2022-09-29 Eliminate limits on nozzle angle
2022-11-09 Nozzle 2
    [base.FCStd, bearing.FCStd, bearing2.FCStd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]
2022-11-10 Hall effect sensor glitch during homing
    [base.FCStd]
2025-03-31 inlining some functions, adding 2 more presets, trying to increase the pitch resolution
